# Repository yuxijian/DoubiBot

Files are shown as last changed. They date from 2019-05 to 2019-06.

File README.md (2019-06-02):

# DoubiBot


DoubiBot是一个基于ESP8266的手写机器人，可以实现手动报时和天气预报等功能，你也可以把它当作一个通用机械臂。



**仓库包含制作DoubiBot所需要的全部资料，包括：**

- PCB文件和原理图

- Arduino固件源码和相关库文件

- 3D模型文件

- DWG激光切割文件

**如果不自己制作PCB也可以直接用NodeMcu替代↓**

  

**需要额外准备的材料：**

- 9g舵机3个 **共10元**

- 白板笔1支 **共3元**

- NodeMcu ESP8266开发板一块 **15元**

- 舵机拉杆 1.2MM Z字钢丝 **1元**

- M3x3 平头螺丝若干

- M3 螺母若干

- M3x12 螺丝若干

- M3x6 T型对接螺丝若干

- 亚克力激光切割零件一批 **根据跟加工店老板的熟悉程度0~100元不等**

详细教程可以参考这篇文章：

[稚晖：如何制作一支带逗比功能的笔](https://zhuanlan.zhihu.com/p/67700105)

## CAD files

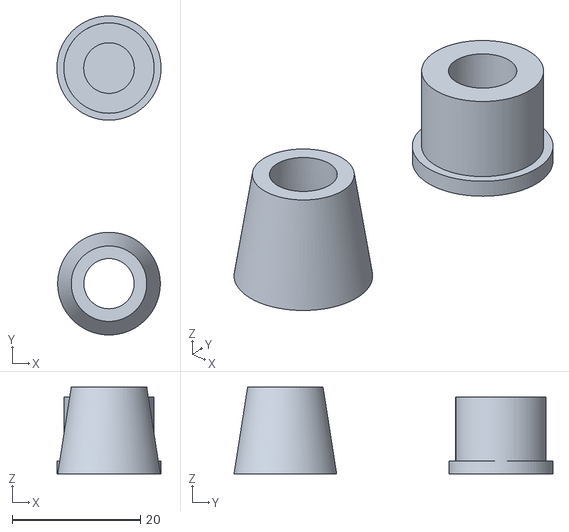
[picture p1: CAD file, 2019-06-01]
Model/3D打印件/笔帽&笔架.stl
16.2 x 49.7 x 13.5

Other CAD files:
Model/亚克力切割/b3-白色1mm.dwg
Model/亚克力切割/b4-白色2mm.dwg
Model/亚克力切割/b2-透明3mm.dwg
Model/亚克力切割/b1-白色3mm.dwg

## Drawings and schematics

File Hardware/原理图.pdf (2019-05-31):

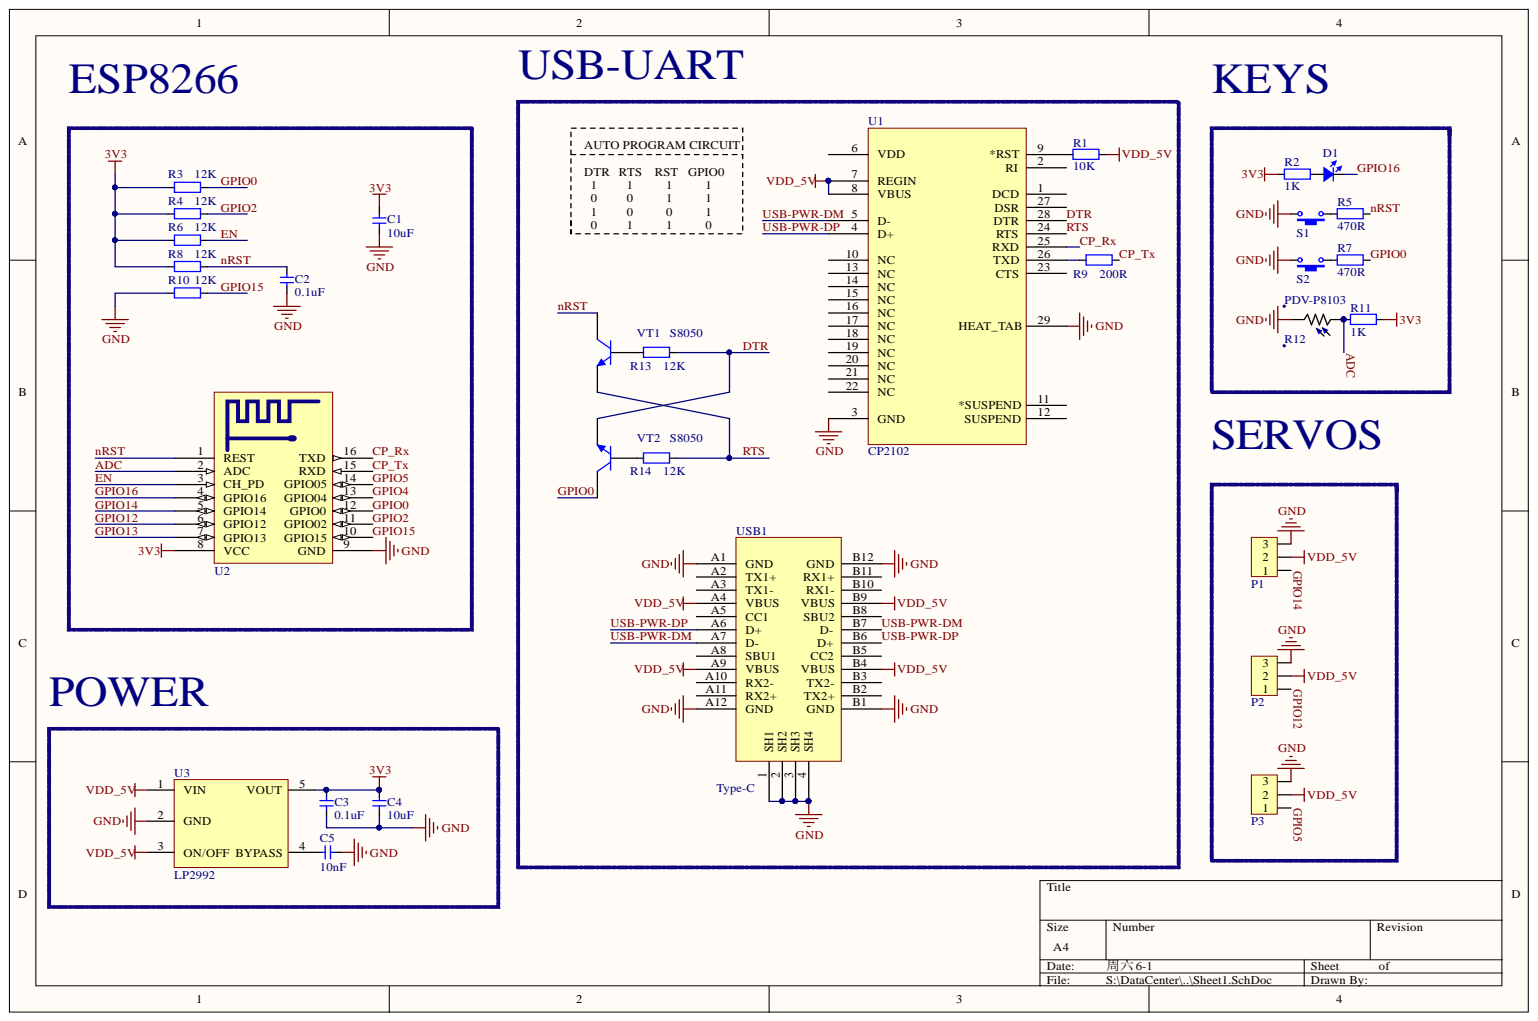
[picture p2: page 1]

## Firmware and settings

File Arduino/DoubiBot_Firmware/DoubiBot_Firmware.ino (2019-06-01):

#include "Control.h"
#include "TimeUtils.h"
#include "WeatherUtils.h"

//#define DRAW_WEATHER
//#define DRAW_TIME


const char* SSID = "***";				// 要连接的WiFi的名称
const char* PASSWORD = "***";		// 要连接的WiFi的密码
const char* CITY = "shanghai";

Control control(12, 5, 14);

TimeClient timeClient;
TimeData timeData, lastTime, lastWeather;

WeatherClient weatherClient;
WeatherData weatherData;

void setup()
{
	// uncommet this to do calibration, code will be blocked here
	control.Calibrate();

	Serial.begin(115200);

	WiFi.mode(WIFI_STA);     //设置ESP8266工作模式
	WiFi.begin(SSID, PASSWORD);

	while (WiFi.status() != WL_CONNECTED)
	{
		delay(500);
		Serial.print(".");
	}

	Serial.println("\nWiFi connected");
	Serial.print("IP address: ");
	Serial.println(WiFi.localIP());

	control.GoHome();
}

void loop()
{
	// Serial CMD check, run this as often as possible
	control.CmdRoutine();

	// Get time through internet
	timeClient.UpdateTime(timeData);

	Serial.print("Now the time is ");
	Serial.print(timeData.hours);
	Serial.print(":");
	Serial.println(timeData.minutes);

#ifdef DRAW_TIME
	// Draw time every minute
	if (timeData.minutes != lastTime.minutes || timeData.hours != lastTime.hours)
	{
		control.Lift(LIFT_STATE::ON_DRAW);

		control.Clear();
		control.DrawNumber(5, 30, timeData.hours / 10, 1);
		control.DrawNumber(19, 30, timeData.hours % 10, 1);
		control.DrawNumber(28, 30, 11, 0.9);
		control.DrawNumber(34, 30, timeData.minutes / 10, 1);
		control.DrawNumber(48, 30, timeData.minutes % 10, 1);

		control.Lift(LIFT_STATE::LIFTED);
		control.GoTo(74.2, 45.5);
		control.Lift(LIFT_STATE::BETWEEN_NUMS);

		lastTime = timeData;
	}
#endif

#ifdef DRAW_WEATHER
	// Get weather through internet
	if (true || timeData.hours != lastWeather.hours)
	{
		lastWeather.hours = timeData.hours;

		weatherClient.UpdateWeather(CITY, weatherData);
		Serial.print("City: ");
		Serial.print(weatherData.city);
		Serial.print("   Weather: ");
		Serial.print(weatherData.weather);
		Serial.print("   Temp: ");
		Serial.println(weatherData.temp);

		String weather_type(weatherData.weather);

		if (true || weather_type.indexOf("sunny") > -1)
		{
			control.Clear();

			control.DrawWeatherIcon(10, 26, 1, 1);
			control.Lift(LIFT_STATE::BETWEEN_NUMS);

			control.DrawNumber(39, 27, weatherData.temp / 10, 0.8);
			control.DrawNumber(53, 27, weatherData.temp % 10, 0.8);

			control.GoHome();
		}
		else if (weather_type.indexOf("cloudy") > -1)
		{
			// ToDo
		}
		// other...
	}
#endif

	delay(1000);
}

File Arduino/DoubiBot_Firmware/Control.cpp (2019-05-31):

#include "Control.h"

Control::Control(int pin_lift, int pin_left, int pin_right)
{
	GoTo(35, 50);

	servo_lift.attach(pin_lift);  //  lifting servo
	servo_left.attach(pin_left);  //  left servo
	servo_right.attach(pin_right);  //  right servo
	delay(100);

	Lift(LIFT_STATE::BETWEEN_NUMS);
	GoTo(35, 50);
}

void Control::Calibrate()
{
	while (true)
	{
		GoTo(-3, 29.2);
		delay(1000);
		GoTo(74.1, 28);
		delay(1000);
	}
}

bool Control::CmdRoutine()
{
	int p, x, y;

	while (Serial.available() > 0)
	{
		char nullByte = char(Serial.read());
		if (nullByte == '\n')
		{
			comdata[data_p] = nullByte;
			data_p = 0;

			switch (comdata[0])
			{
			case 'G':
				strtok(comdata, ",");
				x = atoi(strtok(NULL, ","));
				y = atoi(strtok(NULL, "\n"));

				x = constrain(x, 5, 70);
				y = constrain(y, 20, 50);
				GoTo(x, y);

				Serial.println("Ok");
				break;

			case 'L':
				strtok(comdata, ",");
				x = atoi(strtok(NULL, ","));

				switch (x)
				{
				case 1:
					Lift(LIFT_STATE::ON_DRAW);
					Serial.println("Lift state: ON_DRAW");
					break;

				case 2:
					Lift(LIFT_STATE::BETWEEN_NUMS);
					Serial.println("Lift state: BETWEEN_NUMS");
					break;

				case 3:
					Lift(LIFT_STATE::LIFTED);
					Serial.println("Lift state: LIFTED");
					break;
				default:
					break;
				}

				break;

			case 'H':
				GoHome();
				Serial.println("Ok, homed");

				break;
			}
		}
		else
		{
			comdata[data_p] = nullByte;
			data_p++;
		}
	}

	return true;
}


void Control::DrawNumber(float bx, float by, int num, float scale)
{
	switch (num)
	{

	case 0:
		GoTo(bx + 12 * scale, by + 6 * scale);
		Lift(LIFT_STATE::ON_DRAW);
		circleAntiClockwise(bx + 7 * scale, by + 10 * scale, 10 * scale, -0.8, 6.7, 0.5);
		Lift(LIFT_STATE::BETWEEN_NUMS);
		break;
	case 1:
		GoTo(bx + 3 * scale, by + 15 * scale);
		Lift(LIFT_STATE::ON_DRAW);
		GoTo(bx + 10 * scale, by + 20 * scale);
		GoTo(bx + 10 * scale, by + 0 * scale);
		Lift(LIFT_STATE::BETWEEN_NUMS);
		break;
	case 2:
		GoTo(bx + 2 * scale, by + 12 * scale);
		Lift(LIFT_STATE::ON_DRAW);
		circleClockwise(bx + 8 * scale, by + 14 * scale, 6 * scale, 3, -1.6, 1);
		GoTo(bx + 1 * scale, by + 0 * scale);
		GoTo(bx + 12 * scale, by + 0 * scale);
		Lift(LIFT_STATE::BETWEEN_NUMS);
		break;
	case 3:
		GoTo(bx + 2 * scale, by + 17 * scale);
		Lift(LIFT_STATE::ON_DRAW);
		circleClockwise(bx + 5 * scale, by + 15 * scale, 5 * scale, 3, -2, 1);
		circleClockwise(bx + 5 * scale, by + 5 * scale, 5 * scale, 1.57, -3, 1);
		Lift(LIFT_STATE::BETWEEN_NUMS);
		break;
	case 4:
		GoTo(bx + 10 * scale, by + 0 * scale);
		Lift(LIFT_STATE::ON_DRAW);
		GoTo(bx + 10 * scale, by + 20 * scale);
		GoTo(bx + 2 * scale, by + 6 * scale);
		GoTo(bx + 12 * scale, by + 6 * scale);
		Lift(LIFT_STATE::BETWEEN_NUMS);
		break;
	case 5:
		GoTo(bx + 2 * scale, by + 5 * scale);
		Lift(LIFT_STATE::ON_DRAW);
		circleAntiClockwise(bx + 5 * scale, by + 6 * scale, 6 * scale, -2.5, 2, 1);
		GoTo(bx + 5 * scale, by + 20 * scale);
		GoTo(bx + 12 * scale, by + 20 * scale);
		Lift(LIFT_STATE::BETWEEN_NUMS);
		break;
	case 6:
		GoTo(bx + 2 * scale, by + 10 * scale);
		Lift(LIFT_STATE::ON_DRAW);
		circleClockwise(bx + 7 * scale, by + 6 * scale, 6 * scale, 2, -4.4, 1);
		GoTo(bx + 11 * scale, by + 20 * scale);
		Lift(LIFT_STATE::BETWEEN_NUMS);
		break;
	case 7:
		GoTo(bx + 2 * scale, by + 20 * scale);
		Lift(LIFT_STATE::ON_DRAW);
		GoTo(bx + 12 * scale, by + 20 * scale);
		GoTo(bx + 2 * scale, by + 0);
		Lift(LIFT_STATE::BETWEEN_NUMS);
		break;
	case 8:
		GoTo(bx + 5 * scale, by + 10 * scale);
		Lift(LIFT_STATE::ON_DRAW);
		circleClockwise(bx + 5 * scale, by + 15 * scale, 5 * scale, 4.7, -1.6, 1);
		circleAntiClockwise(bx + 5 * scale, by + 5 * scale, 5 * scale, -4.7, 2, 1);
		Lift(LIFT_STATE::BETWEEN_NUMS);
		break;

	case 9:
		GoTo(bx + 9 * scale, by + 11 * scale);
		Lift(LIFT_STATE::ON_DRAW);
		circleClockwise(bx + 7 * scale, by + 15 * scale, 5 * scale, 4, -0.5, 1);
		GoTo(bx + 5 * scale, by + 0);
		Lift(LIFT_STATE::BETWEEN_NUMS);
		break;

	case 111:

		Lift(LIFT_STATE::ON_DRAW);
		GoTo(70, 46);
		GoTo(65, 43);

		GoTo(65, 49);
		GoTo(5, 49);
		GoTo(5, 45);
		GoTo(65, 45);
		GoTo(65, 40);

		GoTo(5, 40);
		GoTo(5, 35);
		GoTo(65, 35);
		GoTo(65, 30);

		GoTo(5, 30);
		GoTo(5, 25);
		GoTo(65, 25);
		GoTo(65, 20);

		GoTo(5, 20);
		GoTo(60, 44);

		GoTo(75.2, 47);
		Lift(LIFT_STATE::LIFTED);

		break;

	case 11:
		GoTo(bx + 5 * scale, by + 15 * scale);
		Lift(LIFT_STATE::ON_DRAW);
		circleAntiClockwise(bx + 5 * scale, by + 15 * scale, 0.1 * scale, 1, -1, 1);
		delay(200);
		Lift(LIFT_STATE::BETWEEN_NUMS);
		GoTo(bx + 5 * scale, by + 5 * scale);
		Lift(LIFT_STATE::ON_DRAW);
		circleAntiClockwise(bx + 5 * scale, by + 5 * scale, 0.1 * scale, 1, -1, 1);
		delay(200);
		Lift(LIFT_STATE::BETWEEN_NUMS);
		break;

	}
}

void Control::DrawWeatherIcon(float bx, float by, int type, float scale)
{
	switch (type)
	{
	case 1: //sunny
		GoTo(bx + 10 * scale, by + 10 * scale);
		Lift(LIFT_STATE::ON_DRAW);
		circleAntiClockwise(bx + 10 * scale, by + 10 * scale, 8 * scale, -0.8, 7, 1);
		Lift(LIFT_STATE::BETWEEN_NUMS);

		GoTo(bx + 10 * scale, by + 22 * scale);
		Lift(LIFT_STATE::ON_DRAW);
		delay(200);
		Lift(LIFT_STATE::BETWEEN_NUMS);
		GoTo(bx + 19 * scale, by + 19 * scale);
		Lift(LIFT_STATE::ON_DRAW);
		delay(200);
		Lift(LIFT_STATE::BETWEEN_NUMS);
		GoTo(bx + 22 * scale, by + 10 * scale);
		Lift(LIFT_STATE::ON_DRAW);
		delay(200);
		Lift(LIFT_STATE::BETWEEN_NUMS);
		GoTo(bx + 19 * scale, by + 1 * scale);
		Lift(LIFT_STATE::ON_DRAW);
		delay(200);
		Lift(LIFT_STATE::BETWEEN_NUMS);
		GoTo(bx + 10 * scale, by - 2 * scale);
		Lift(LIFT_STATE::ON_DRAW);
		delay(200);
		Lift(LIFT_STATE::BETWEEN_NUMS);
		GoTo(bx + 1 * scale, by + 1 * scale);
		Lift(LIFT_STATE::ON_DRAW);
		delay(200);
		Lift(LIFT_STATE::BETWEEN_NUMS);
		GoTo(bx + -2 * scale, by + 10 * scale);
		Lift(LIFT_STATE::ON_DRAW);
		delay(200);
		Lift(LIFT_STATE::BETWEEN_NUMS);
		GoTo(bx + 1 * scale, by + 19 * scale);
		Lift(LIFT_STATE::ON_DRAW);
		delay(200);
		break;
	}
}

void Control::Lift(LIFT_STATE s)
{
	int target;

	switch (s)
	{
	case LIFT_STATE::ON_DRAW:
		target = LIFT0;
		break;
	case LIFT_STATE::BETWEEN_NUMS:
		target = LIFT1;
		break;
	case LIFT_STATE::LIFTED:
		target = LIFT2;
		break;
	}

	if (servoLift > target)
	{
		while (servoLift > target)
		{
			servoLift--;
			servo_lift.writeMicroseconds(servoLift);
			delayMicroseconds(LIFTSPEED);
		}
	}
	else
	{
		while (servoLift < target)
		{
			servoLift++;
			servo_lift.writeMicroseconds(servoLift);
			delayMicroseconds(LIFTSPEED);
		}

	}
}

void Control::circleClockwise(float bx, float by, float radius, int start, int ende, float sqee)
{
	float inkr = -0.05;
	float count = 0;

	do
	{
		GoTo(sqee * radius * cos(start + count) + bx,
			radius * sin(start + count) + by);
		count += inkr;
	} while ((start + count) > ende);

}
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

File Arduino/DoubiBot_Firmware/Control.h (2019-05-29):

#pragma once
#include <Servo.h>


enum LIFT_STATE
{
	ON_DRAW,
	BETWEEN_NUMS,
	LIFTED
};

class Control
{
public:
	Control(int pin_lift, int pin_left, int pin_right);
	void Calibrate();

	void DrawNumber(float bx, float by, int num, float scale);
	void DrawWeatherIcon(float bx, float by, int type, float scale);

	void Lift(LIFT_STATE s);
	void GoTo(double pX, double pY);
	void GoHome();
	void Clear();

	bool CmdRoutine();


private:
	// When in calibration mode, adjust the following factor until the servos move exactly 90 degrees
	int SERVOFAKTOR = 550;

	// Zero-position of left and right servo
	// When in calibration mode, adjust the NULL-values so that the servo arms are at all times parallel
	// either to the X or Y axis
	int SERVOLEFTNULL = 1800;
	int SERVORIGHTNULL = 1100;

	int LIFT0 = 1650;
	int LIFT1 = 1550;
	int LIFT2 = 1350;


	int SERVOPINLIFT = 12;
	int SERVOPINLEFT = 5;
	int SERVOPINRIGHT = 14;

	// speed of liftimg arm, higher is slower
	int LIFTSPEED = 1500;

	// 悬臂的长度，根据图纸测量，无需改变
	int L1 = 35;
	int L2 = 57.2;
	int L3 = 13;

	// 左右舵机轴心的位置，根据图纸测量，无需改变
	int O1X = 22;
	int O1Y = -25;
	int O2X = 47;
	int O2Y = -25;

	volatile double lastX = 35;
	volatile double lastY = 50;
	volatile int servoLift = 1500;

	Servo servo_lift;
	Servo servo_left;
	Servo servo_right;

	char comdata[256], data_p; //串口缓存数据
	long time;


	void circleClockwise(float bx, float by, float radius, int start, int ende, float sqee);

	void circleAntiClockwise(float bx, float by, float radius, int start, int ende, float sqee);


	double return_angle(double a, double b, double c);

	void set_XY(double Tx, double Ty);
};

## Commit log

2019-05-16 初始化仓库
2019-05-16 添加NTP时间功能
2019-05-31 release version
    [DoubiBot_PCB.PcbDoc]
2019-06-01 bug fix
    [b1-白色3mm.dwg, b2-透明3mm.dwg, b3-白色1mm.dwg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]
2019-06-02 添加说明
